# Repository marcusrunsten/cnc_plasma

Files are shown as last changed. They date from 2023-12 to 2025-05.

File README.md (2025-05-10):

# cnc_plasma
Plans and such for my CNC plasma project, https://www.runstenracing.se/?cat=61

To see the plasma in action, https://www.youtube.com/watch?v=OwQSaWDesY0

The plasma is using 2 Nema24 motors to run the Y axis, and Nema17 motors on X and Z.<br>
I'm using a SKR controller for a 3D printer to run the stepper motors and a Raspberry Pi with Klipper for the software interface.<br>
I've configured klipper to trick the software into running the scrape start for the plasma on each start and I've written a custom POST processor for Fusion360 to export the gcode to the cutter.

I'll supply the STEP file for the hardware and the POST processor now and I'll add the customization for the klipper software later on.

Bill of materials
-----------------

**Frame**

- 2x1000mm 40x40 aluminium extrusion
- 3x1000mm 20x40 aluminium extrusion
- 1x300mm 20x40 aluminium extrusion for z-axis (?)
- 9x v-slot wheel with bearings for M5 bolt
- 3x offset adjusting nut for v-slot wheel
- 3x 2100mm GT2 6mm belt
- 1x 700mm GT2 6mm belt
- 4x 16T GT2 6mm pulleys with matching hole diameter to the chosen stepper motors
- 4x GT2 6mm idlers with bearings for M5 bolt
- 4x 9mm (?) magnets for the torch holder

**Electronics**

- SKR or similar 3D printer control board
  - Compatible with klipper
  - Supporting at least 4 separate axis/stepper motors
  - At least one digital output channel
  - At least one digital input channel
- Raspberry pi or similar able to run Klipper with Moonraker frontend
- 5v relay or similar FET to drive the plasma cutter trigger
- Microswitch for z sensing (will add details later)
- 2x Nema24 or similar steppers motors for Z axis (other sizes work just as well but need new design for mount)
- 2x Nema17 or similar steppers for X and Z axis

**Mounting hardware**

- M5 bolts, details to be added later
- M5 t-slot nuts, details to be added later
- 4xM12 bolts for mounting the 40x40 extrusions
- Printed or milled mounting hardware as per the CAD file
- Suitable cable chains for cable routing, at least 2m

**Plasma cutter**

The requirements of the plasma cutter depends on what material you want to cut. I'm using a Cut60 with a maximum power of 60A and touch start.<br>
The benefit of using touch instead of HF start is that it's less prone to causing problems with the electronics due to RF noise. Still I have some problems of the controller getting brown-outs at more than 42A power which I'm sure can be remedied with shielding and better cable routing but so far I have managed to cut what I've needed as it is.

I've installed a straight plasma torch on my cutter which is nice but not necessary. To use the standard torch a new holder needs to be designed though.<br>
I've cut the trigger feed to the torch and installed a connector to route it to the relay instead of the trigger on the torch. The relay is controlled by a digital output pin on the SKR control board to start and stop the plasma.

**TODO::**

Check the size of the magnets on the torch holder<br>
Count M5 bolts and lengths<br>
Count M5 t-slot nuts<br>
Get the details of the micro switch for the z-limit<br>
Measure the length of the Z extrusion<br>

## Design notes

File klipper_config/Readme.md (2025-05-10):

This is the klipper configuration for the plasma cutter.

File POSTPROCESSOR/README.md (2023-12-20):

This is the custom Fusion360 POST processor for the plasma. Working with the klipper configuration I've made for the plasma.

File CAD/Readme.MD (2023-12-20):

This is the STEP file for the CNC plasma

I've done a quick cleanup of the file and all parts named _NOTUSE are not to be used. Most of the custom parts I've milled from aluminium but a good 3D print should work just as fine.

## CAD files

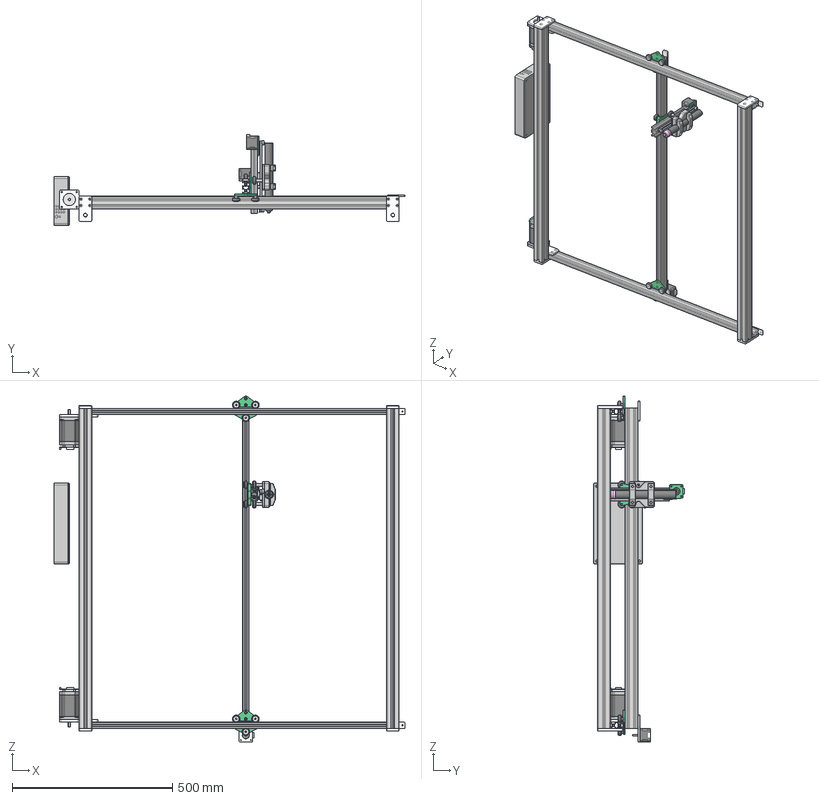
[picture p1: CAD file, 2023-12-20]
CAD/runsten_plasma_v1.step
1095.9 x 285.0 x 1080.0 mm
_LCF6-2040-50 (1)
Nut x 3
Washers
V-slot wheel x 9
StepperHolder
Zstepper
IdlerHolder (1)
Washers (1) x 2
_LCF6-2040-50 (2)
_LCF6-2040-50 (2) (1)
YIdlerHolder x 2
Nema24_XY_Stepper (1)
StepperMount (1)
Nema24_XY_Stepper (1)(Mirror)
StepperMount _2
Bracket (1) x 4
_GNFS8-4040-50 (1) x 2
Lid
2040_rail (1)
LimitSwitch (1)
Torch (1)
Zstepper (1)
BeltWheel (1)
BeltWheel (2)
StepperMount (3)
V-slot wheel (1)
V-slot wheel (2)
V-slot wheel (3)
Distance
Distance (1)
Distance (2)
Plate
SpringPusher
Magnet x 4
BeltSled
TorchMount_2

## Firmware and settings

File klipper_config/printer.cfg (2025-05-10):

# This file contains common pin mappings for the BIGTREETECH SKR mini
# E3 v3.0. To use this config, the firmware should be compiled for the
# STM32G0B1 with a "8KiB bootloader" and USB communication/USART.

# The "make flash" command does not work on the SKR mini E3. Instead,
# after running "make", copy the generated "out/klipper.bin" file to a
# file named "firmware.bin" on an SD card and then restart the SKR
# mini E3 with that SD card.

# See docs/Config_Reference.md for a description of parameters.

[include mainsail.cfg]
[include plasmascripts.cfg]

[stepper_x]
step_pin: PB13
dir_pin: !PB12
enable_pin: !PB14
microsteps: 16
rotation_distance: 40
endstop_pin: ^!PC0
position_endstop: 0
position_min: -100
position_max: 900
homing_speed: 20

[tmc2209 stepper_x]
uart_pin: PC11
tx_pin: PC10
uart_address: 0
run_current: 0.720
stealthchop_threshold: 999999

[stepper_y]
step_pin: PB10
dir_pin: PB2
enable_pin: !PB11
microsteps: 256
rotation_distance: 40
endstop_pin: ^!PC1
position_endstop: 0
position_min: -100
position_max: 900
homing_speed: 20

[tmc2209 stepper_y]
uart_pin: PC11
tx_pin: PC10
uart_address: 2
run_current: 0.580 #0.580
hold_current: 0.500
#stealthchop_threshold: 999999

[stepper_y1]
step_pin: PB3
dir_pin: PB4
enable_pin: !PD1
microsteps: 256
rotation_distance: 40

[tmc2209 stepper_y1]
uart_pin: PC11
tx_pin: PC10
uart_address: 3
run_current: 0.580 #0.580
hold_current: 0.500
#stealthchop_threshold: 999999


[stepper_z]
step_pin: PB0
dir_pin: PC5
enable_pin: !PB1
microsteps: 16
rotation_distance: 32
endstop_pin: ^!PC2
position_endstop: 0.0
homing_positive_dir: false
position_max: 20
position_min: -10

[tmc2209 stepper_z]
uart_pin: PC11
tx_pin: PC10
uart_address: 1
run_current: 0.580
hold_current: 0.500
stealthchop_threshold: 999999

#[extruder]
#step_pin: PB3
#dir_pin: !PB4
#enable_pin: !PD1
#microsteps: 16
#rotation_distance: 33.500
#nozzle_diameter: 0.400
#filament_diameter: 1.750
#heater_pin: PC8
#sensor_type: EPCOS 100K B57560G104F
#sensor_pin: PA0
#control: pid
#pid_Kp: 21.527
#pid_Ki: 1.063
#pid_Kd: 108.982
#min_temp: 0
#max_temp: 250

#[tmc2209 extruder]
#uart_pin: PC11
#tx_pin: PC10
#uart_address: 3
#run_current: 0.650
#hold_current: 0.500
#stealthchop_threshold: 999999

#[heater_bed]
#heater_pin: PC9
#sensor_type: ATC Semitec 104GT-2
#sensor_pin: PC4
#control: pid
#pid_Kp: 54.027
#pid_Ki: 0.770
#pid_Kd: 948.182
#min_temp: 0
#max_temp: 130

#[heater_fan controller_fan]
#pin: PB15
#heater: heater_bed
#heater_temp: 45.0

#[heater_fan nozzle_cooling_fan]
#pin: PC7

[fan]
pin: PC6

[mcu]
#serial: /dev/serial/by-id/usb-Klipper_stm32g0b1xx_4D003C000B50345033313820-if00
serial: /dev/ttyACM0
# serial: /dev/ttyAMA0
# restart_method: command

[printer]
kinematics: cartesian
max_velocity: 75
max_accel: 1500 #3000
max_z_velocity: 42
max_z_accel: 100

[board_pins]
aliases:
    # EXP1 header
    EXP1_1=PB5,  EXP1_3=PA9,   EXP1_5=PA10, EXP1_7=PB8, EXP1_9=<GND>,
    EXP1_2=PA15, EXP1_4=<RST>, EXP1_6=PB9,  EXP1_8=PD6, EXP1_10=<5V>


######################################################################
#  BigTreeTech TFT TouchScreen emulated 12864 mode
######################################################################

[display]
lcd_type: emulated_st7920
spi_software_miso_pin: PD8 # status led, Virtual MISO
spi_software_mosi_pin: PD6
spi_software_sclk_pin: PB9
en_pin: PB8
encoder_pins: ^PA10, ^PA9
click_pin: ^!PA15

[output_pin beeper]
pin: PB5

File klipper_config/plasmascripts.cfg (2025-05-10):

# Scripts specific to running the runPlasma cutter

[gcode_arcs]
resolution: 0.4

[output_pin plasma]
pin: PC8

[homing_override]
axes: xy
set_position_x:0
set_position_y:0
gcode:

[gcode_macro ZERO_XY]
gcode:
  G28 x0 y0

[gcode_macro ZERO_Z]
gcode:
  g28 z0
  g1 z7.5

[gcode_macro PLASMA_ON]
gcode:
  #G28 Z0

  {action_respond_info( "Plasma ON" )}
  G0 Z-1.0
  SET_PIN PIN=plasma VALUE=1
  #G4 P200
  G1 Z4.0

[gcode_macro PLASMA_OFF]
gcode:
  {action_respond_info( "Plasma OFF" )}
  SET_PIN PIN=plasma VALUE=0
  G1 Z4.2

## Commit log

2023-12-20 Add files via upload
    Added the stepfile
    [runsten_plasma_v1.step]
2025-05-10 Add files via upload
    Added the klipper configuration
    [mainsail.cfg, plasmascripts.cfg, printer.cfg]
